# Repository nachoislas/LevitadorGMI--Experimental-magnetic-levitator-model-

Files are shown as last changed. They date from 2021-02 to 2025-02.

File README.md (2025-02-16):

# LevitadorGMI
El sistema de control de levitacion magnetica que se desarrolla en este proyecto tiene la finalidad de mantener en estado de levitacion a un objeto por medio de la utilizacion de un electroiman y una placa de control. El primero consta de dos piezas formadas por laminas de acero apiladas: una con forma de “E” , que se encuentra fijada desde arriba y tiene un bobinado de cobre en su rama central.

Link al la publicacion del proyecto [https://rinfi.fi.mdp.edu.ar/handle/123456789/722](https://rinfi.fi.mdp.edu.ar/handle/123456789/722)

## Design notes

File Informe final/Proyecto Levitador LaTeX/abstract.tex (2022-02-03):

%% !TeX spellcheck = en_GB
%
%Multiphase power converters have become a very attractive solution for the current control on high power applications, due to the power dissipation reduction in the active and passive components, and the improvement in the total ripple characteristics.
%
%These applications, which commonly arise in the high-energy physics field, require the control of high current (on the order of kiloamperes) with high precision (on the order of several hundreds of ppm). Additionally, large variations in the current reference and perturbations in the input or output voltages are present. These variations generate transient errors that have to be corrected in several hundreds of microseconds. Given the current level and the technological limitations of the semiconductor devices, the maximum allowable switching frequency implies transient times on the order of a few switching periods. Under these conditions, several requirements arise that cannot be satisfied by the existent current control techniques, due to their limited transient response, or sensitivity to the converter operating point or parasitic elements.
%
%According to these problematics, the present thesis studies the current control in multiphase power converters, and proposes solutions to achieve the transient and precision requirements above mentioned.
%
%The first proposal is the current ripple characterization, as a function of the differences across each phase inductance value. This characterization allows to find expressions for the total ripple that, unlike the methodologies present in the literature, are valid for any number of phases and duty cycle. These expressions allow to calculate others magnitudes, such as peak value, RMS value and the harmonic content of the total current ripple.
%
%The proposed characterization allows to develop a mitigation methodology that significantly improves the total current ripple in practical conditions, with respect to the only methodology present in the literature based on the same principle. This improvement is achieved without significantly increasing the calculation complexity.
%
%Finally, a current control for multiphase power converters is proposed. The proposed control is able to precisely track the current reference, and achieve transient times on the order of a few switching periods, under changes on the current reference or perturbations in the converter input or output voltages.
%
%The proposals have been validated by means of simulations or experimental measurements on a low-scale prototype.

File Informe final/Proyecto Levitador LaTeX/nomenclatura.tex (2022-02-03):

{
\renewcommand{\arraystretch}{0.8}
\begin{longtable}[l]{p{100pt} p{300pt}}
  $CCM$ & Modo de conducción continua \\
  & \textit{(Continous Conduction Mode)} \\
  $DCM$ & Modo de conducción discontinua \\
  & \textit{(Discontinous Conduction Mode)} \\
  $\pwm{x}$ & Señal de comando de la llave de la fase $x$ \\
  $PCMC$ & Control modo corriente pico \\
  & \textit{(Peak Current Mode Control)}\\
  $ACMC$ & Control modo corriente media \\
  & \textit{(Average Current Mode Control)}\\
  $PCPC$ & Control de punto de cruce proyectado \\
  & \textit{(Projected Cross Point Control)}\\    
  $SZCC$ & Control de cruce por cero sincronizado \\
  & \textit{(Synchronized Zero Crossing Control)} \\
  $IGBT$ & Transistor bipolar de puerta aislada \\
  & \textit{(Insulated Gate Bipolar Transistor)} \\
  $MOSFET$ & Transistor de efecto de campo metal-óxido-semiconductor \\ & \textit{(Metal-Oxide-Semiconductor Field-Effect Transistor)} \\
  $FPGA$ & Arreglo de compuertas programable en campo \\
  & \textit{(Field Programmable Gate Array)}
  
%  
%  	$\iref$                        & Referencia de corriente.\\
%  	$i_x$                            & Corriente de la fase $x$.\\
%  	$\ierr{x}$                         & Error de corriente de la fase $x$: $\ierr{x}=\iref-i_x$.                                      \\
%  	$\pwm{x}$                          & Señal de comando de la llave de la fase $x$. \\
%  	$V_{IN}$,$V_0$                   & Tensiones de entrada y salida.\\
%  	$\sync{x}$                  & Señ\\
%  	$T_{Sync}$                       & Synchronization signal period.                                                   \\
%  	$T_S$                            & Switching period.                                                                \\
%  	$t_e(k)$                         & Time error between $i_e$ zero crossing and syncronization signal at instant $k$. \\
%  	$t_{hp}(k+1)$                    & Next semi-period time: $t_{hp}(k+1)=\frac{T_{Sync}}{2}-t_e(k)$                   \\
%  	$t_{sw}(k+1)$                    & Interval between $i_e$ zero crossing and  $\pwm{i}$ switching instant.      \\ 
  \end{longtable}
}

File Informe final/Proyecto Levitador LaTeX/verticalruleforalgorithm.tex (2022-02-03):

% begin vertical rule patch for algorithmicx (http://tex.stackexchange.com/questions/144840/vertical-loop-block-lines-in-algorithmicx-with-noend-option)
\makeatletter
% start with some helper code
% This is the vertical rule that is inserted
    \newcommand*{\algrule}[1][\algorithmicindent]{\makebox[#1][l]{\hspace*{.5em}\thealgruleextra\vrule height \thealgruleheight depth \thealgruledepth}}%
% its height and depth need to be adjustable
\newcommand*{\thealgruleextra}{}
\newcommand*{\thealgruleheight}{.75\baselineskip}
\newcommand*{\thealgruledepth}{.25\baselineskip}

\newcount\ALG@printindent@tempcnta
\def\ALG@printindent{%
    \ifnum \theALG@nested>0% is there anything to print
        \ifx\ALG@text\ALG@x@notext% is this an end group without any text?
            % do nothing
        \else
            \unskip
            \addvspace{-1pt}% FUDGE to make the rules line up
            % draw a rule for each indent level
            \ALG@printindent@tempcnta=1
            \loop
                \algrule[\csname ALG@ind@\the\ALG@printindent@tempcnta\endcsname]%
                \advance \ALG@printindent@tempcnta 1
            \ifnum \ALG@printindent@tempcnta<\numexpr\theALG@nested+1\relax% can't do <=, so add one to RHS and use < instead
            \repeat
        \fi
    \fi
    }%
\usepackage{etoolbox}
% the following line injects our new indent handling code in place of the default spacing
\patchcmd{\ALG@doentity}{\noindent\hskip\ALG@tlm}{\ALG@printindent}{}{\errmessage{failed to patch}}
\makeatother

% the required height and depth are set by measuring the content to be shown
% this means that the content is processed twice
\newbox\statebox
\newcommand{\myState}[1]{%
    \setbox\statebox=\vbox{#1}%
    \edef\thealgruleheight{\dimexpr \the\ht\statebox+1pt\relax}%
    \edef\thealgruledepth{\dimexpr \the\dp\statebox+1pt\relax}%
    \ifdim\thealgruleheight<.75\baselineskip
        \def\thealgruleheight{\dimexpr .75\baselineskip+1pt\relax}%
    \fi
    \ifdim\thealgruledepth<.25\baselineskip
        \def\thealgruledepth{\dimexpr .25\baselineskip+1pt\relax}%
    \fi
    %\showboxdepth=100
    %\showboxbreadth=100
    %\showbox\statebox
    \State #1%
    %\State \usebox\statebox
    %\State \unvbox\statebox
    %reset in case the next command is not wrapped in \myState
    \def\thealgruleheight{\dimexpr .75\baselineskip+1pt\relax}%
    \def\thealgruledepth{\dimexpr .25\baselineskip+1pt\relax}%
}
% end vertical rule patch for algorithmicx

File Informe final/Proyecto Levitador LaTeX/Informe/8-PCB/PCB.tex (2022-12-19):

\chapter{Diseño del circuito impreso} \chapterlabel{Informe/8-PCB} \label{cap:PCB}

%En este capítulo se mencionan los criterios tenidos en cuenta para el diseño del circuito impreso. Además, se muestran los esquemáticos y las imágenes del PCB desarrollados para la implementación de la placa de control mediante el uso del software Altium Designer. 

%Por otra parte, se describen las consideraciones y circuitos utilizados para las fuentes de alimentación del sistema.

En este capítulo se describen las consideraciones y circuitos utilizados para las fuentes de alimentación del sistema. Ademas se mencionan cuales son los conectores, puntos de prueba y jumpers que posee el PCB.

Luego se mencionan los criterios tenidos en cuenta para el diseño del circuito impreso. Además, se muestran los esquemáticos y las imágenes del PCB desarrollados para la implementación de la placa de control mediante el uso del software Altium Designer.

\section{Fuentes de alimentación}

\subsection{Fuente de alimentación externa de 24 V}

La fuente externa se encarga de alimentar todo el circuito. Debe ser capaz de suministrar $24\:V$ y hasta $30\:A$. Para ello se puede utilizar una fuente de laboratorio o baterías. Esta fuente se conecta a la placa de control mediante una bornera dispuesta en el borde del PCB. Además, se agrega un fusible para proteger la placa ante sobre-consumo y un diodo para evitar que se dañe cuando se ingresa con polaridad invertida.

\subsection{Fuente de alimentación interna de 12 V}

La fuente de $12\:V$ se encarga de alimentar al regulador de $5\:V$ y al \textsl{driver} del puente H. Debido a los bajos consumos de potencia y bajo costo, se utiliza una fuente lineal. Por lo tanto, se decide utilizar el integrado L78M12CDT-TR.

\subsection{Fuente de alimentación interna de 5 V}

La fuente de $5\:V$ se encarga de alimentar los operacionales, el sensor de efecto Hall, el inversor y el regulador de tensión de $2.5\:V$. Debido a los bajos consumos de potencia y bajo costo, se utiliza una fuente lineal. Por lo tanto, se decide utilizar el integrado L78M05CDT.

\section{Conexión entre placa de control y microcontrolador}

Se utiliza un conector tipo DB9 hembra como vía de conexión para las distintas salidas y entradas digitales. Además, en la placa se dispone de un led que se enciende cuando  se detecta una correcta conexión con el microcontrolador.

\section{Puntos de prueba y jumpers}

Se agregan puntos de prueba sobre el PCB para poder medir señales de interés como las de control de los gates de los MOSFET del puente H, la salida del comparador con histéresis, la salida del derivador en la etapa del estimador, entre otros. Cada punto de prueba está referenciado en los esquemáticos como TP.

Por otro lado, se agregan jumpers con el objetivo de hacer mediciones a cada etapa por separado. Cada uno de ellos está referenciado en los esquemáticos como P.

\section{Esquemáticos}

\subsection{Principal}
\begin{figure}[H]
	\centering
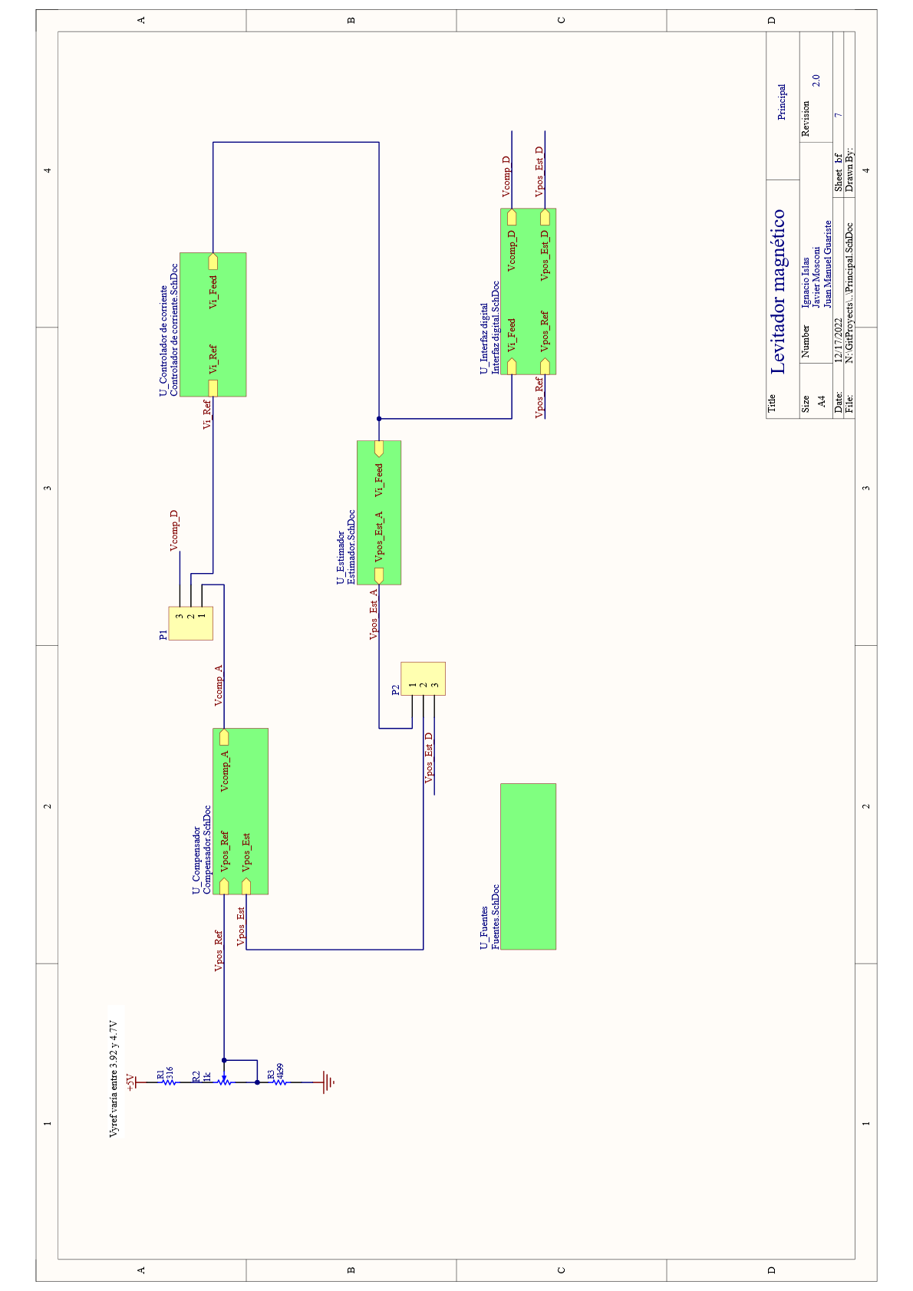
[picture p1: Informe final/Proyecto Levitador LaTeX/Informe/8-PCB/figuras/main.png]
	
	%\caption{Diagrama en bloques de la implementación digital.}
	\label{fig:main}
\end{figure}

\subsection{Controlador de corriente}
\begin{figure}[H]
	\centering
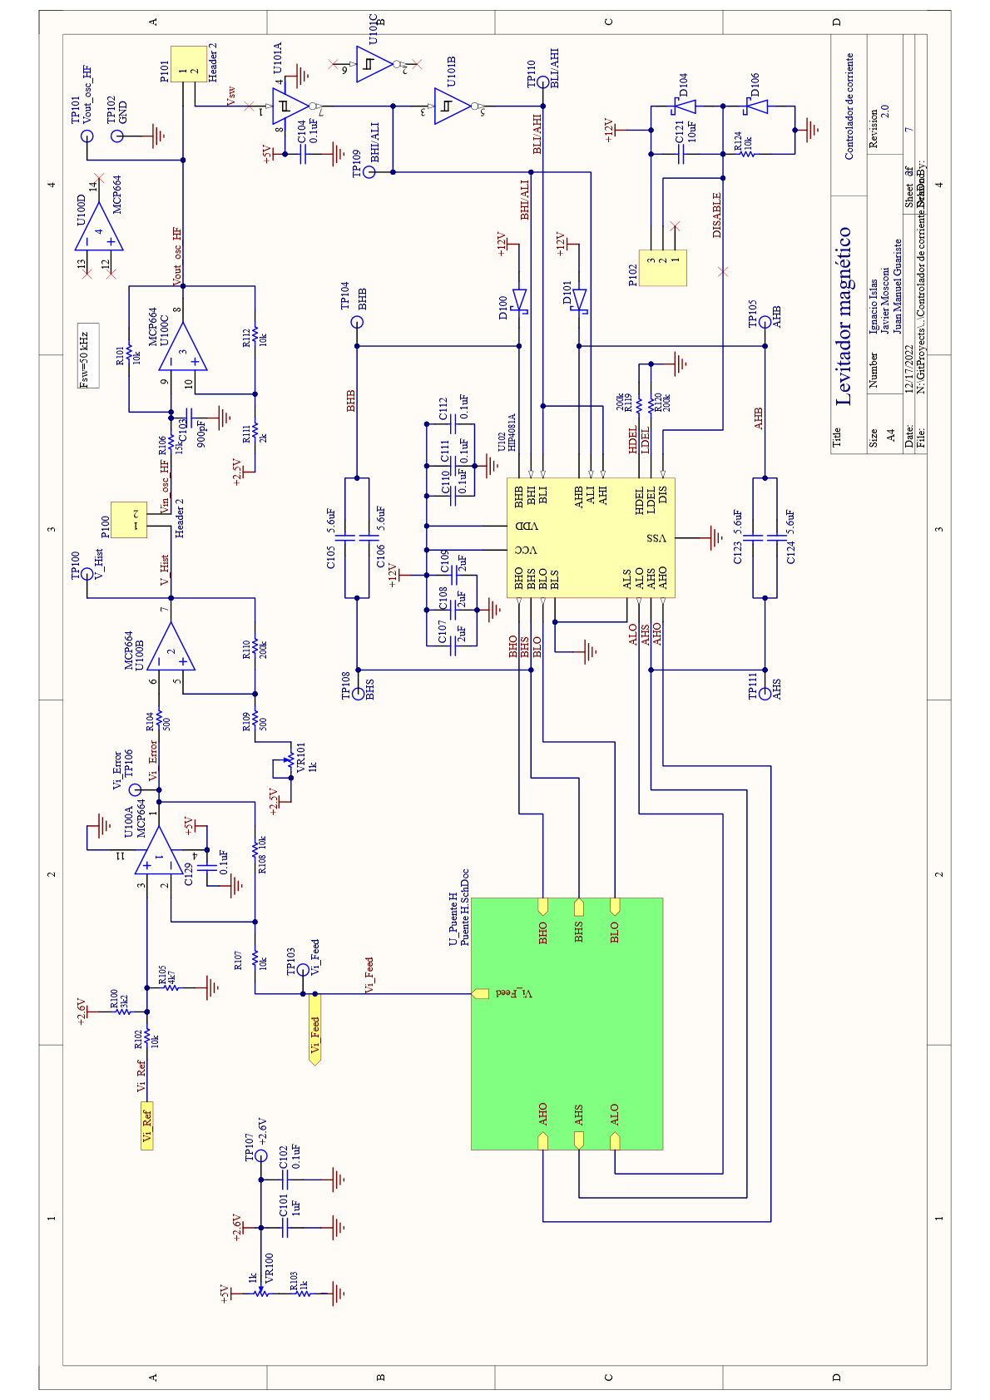
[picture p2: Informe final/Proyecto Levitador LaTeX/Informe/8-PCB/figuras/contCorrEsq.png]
	
	%\caption{Diagrama en bloques de la implementación digital.}
	\label{fig:contCorrEsq}
\end{figure}

\subsection{Puente H}
\begin{figure}[H]
	\centering
	
	%\caption{Diagrama en bloques de la implementación digital.}
	\label{fig:PuenteH}
\end{figure}

\subsection{Compensador analógico}
\begin{figure}[H]
	\centering
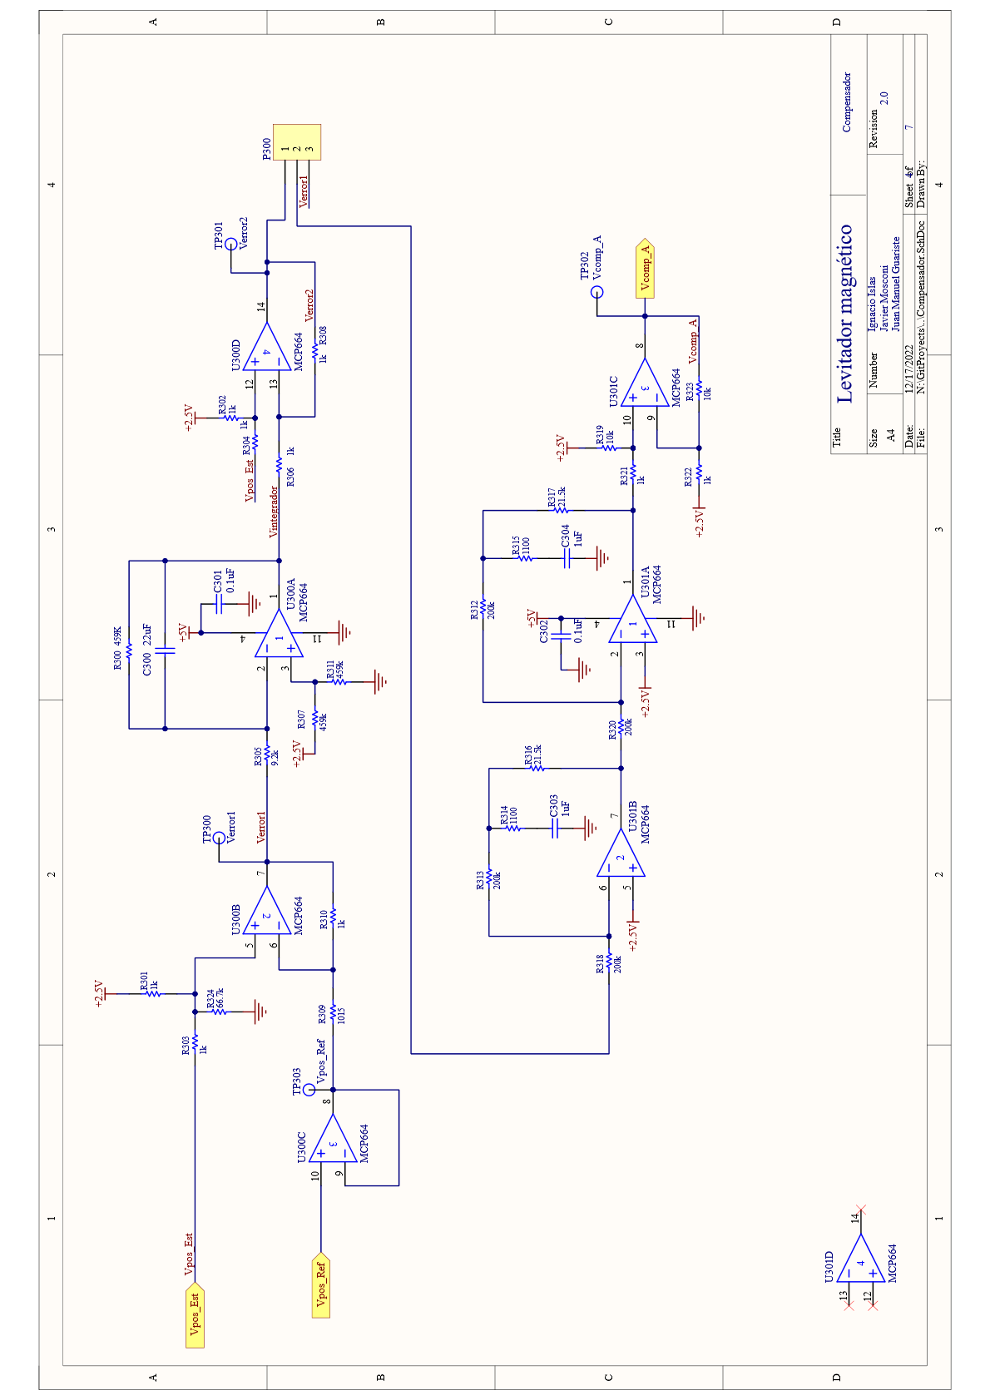
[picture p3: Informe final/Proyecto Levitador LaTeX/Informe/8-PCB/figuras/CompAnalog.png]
	
	%\caption{Diagrama en bloques de la implementación digital.}
	\label{fig:CompAnalog}
\end{figure}

\subsection{Estimador analógico}
\begin{figure}[H]
	\centering
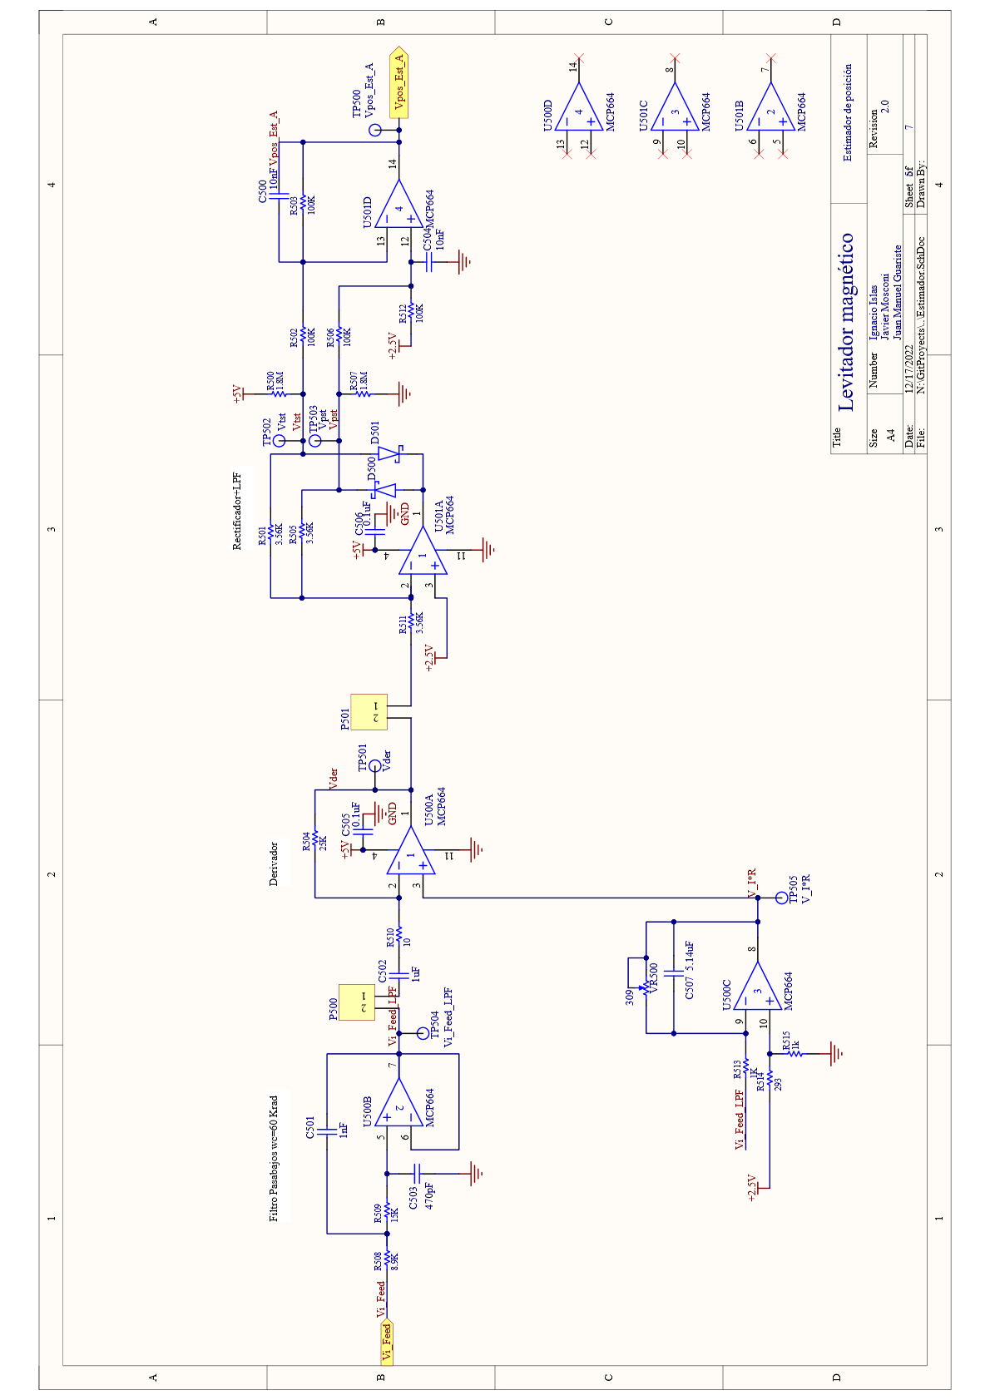
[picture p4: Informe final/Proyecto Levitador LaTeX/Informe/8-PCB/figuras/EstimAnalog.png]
	
	%\caption{Diagrama en bloques de la implementación digital.}
	\label{fig:EstimAnalog}
\end{figure}

\subsection{Interfaz con microcontrolador}
\begin{figure}[H]
	\centering
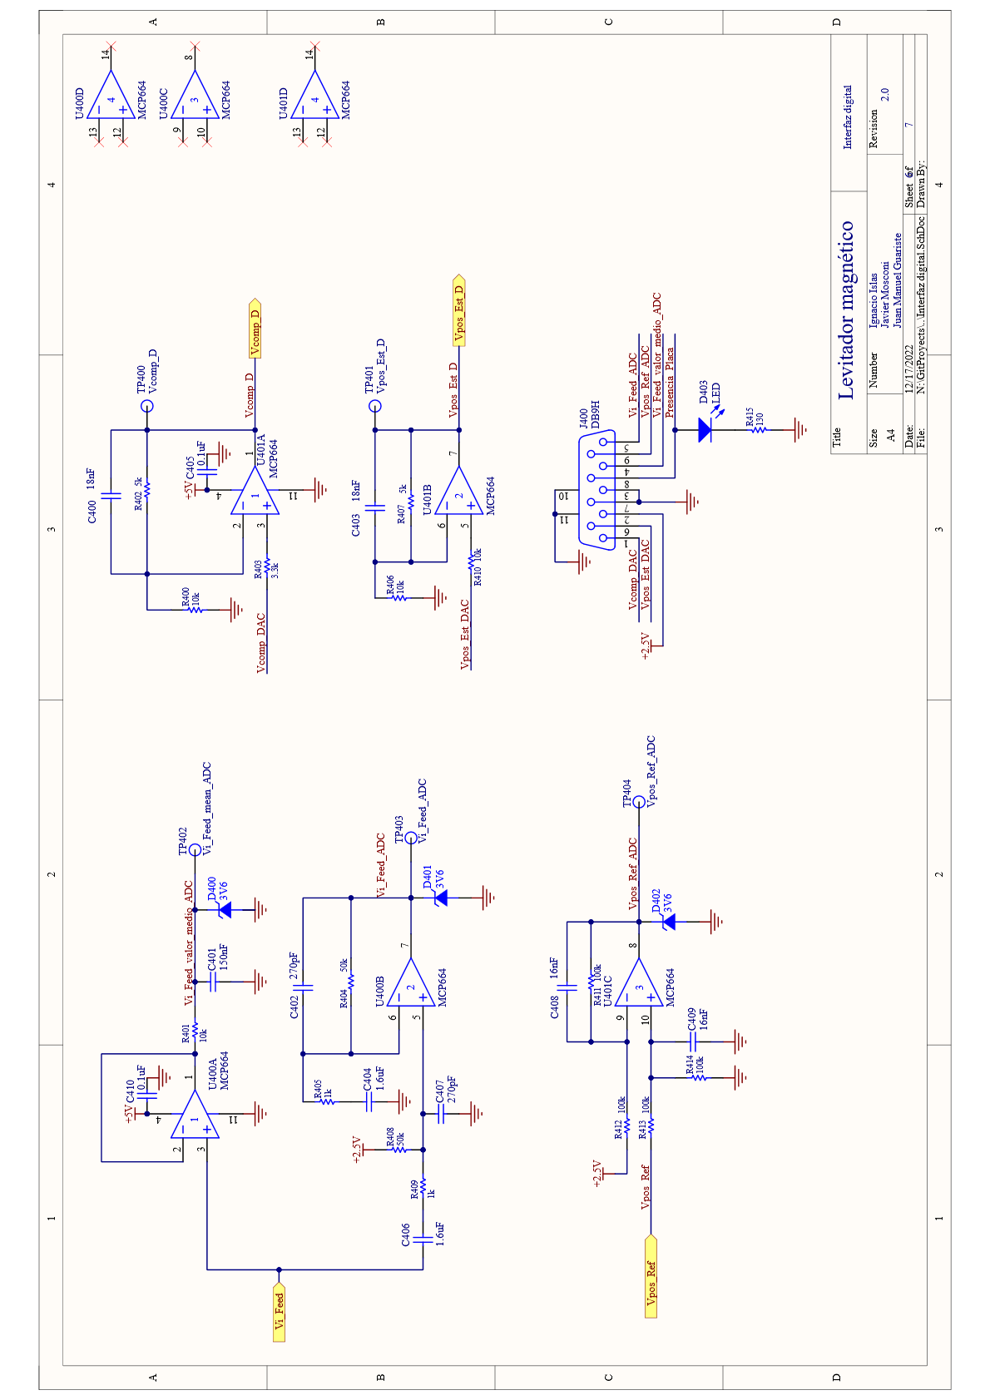
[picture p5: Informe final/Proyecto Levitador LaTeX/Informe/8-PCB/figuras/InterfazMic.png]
	
	%\caption{Diagrama en bloques de la implementación digital.}
	\label{fig:InterfazMic}
\end{figure}

\subsection{Fuentes de alimentación}
\begin{figure}[H]
	\centering
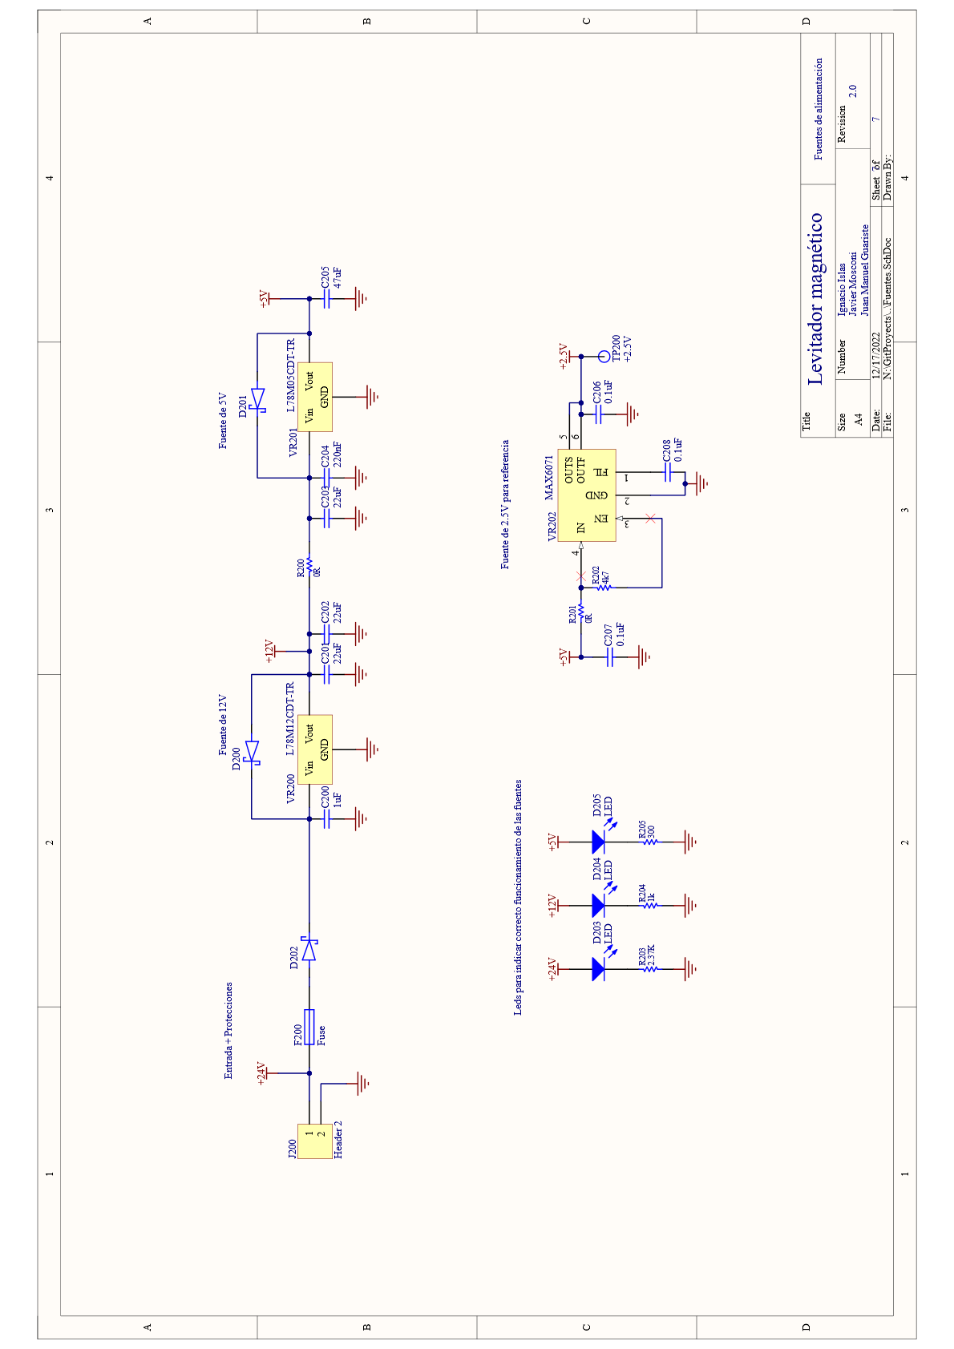
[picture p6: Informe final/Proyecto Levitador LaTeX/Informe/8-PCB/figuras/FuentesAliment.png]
	
	%\caption{Diagrama en bloques de la implementación digital.}
	\label{fig:FuentesAliment}
\end{figure}

\section{PCB}
\subsection{Consideraciones para el diseño del PCB}
Para el diseño del PCB se tuvieron en cuenta los siguientes aspectos:

\begin{itemize}
	\item Se realizó el diseño en una placa de 2 capas para reducir el costo de fabricación.
	\item Se utilizó un plano de masa para la etapa de potencia y otro para el resto del circuito. Se intentó reducir al mínimo las conexiones entre ambos planos con el objetivo de disminuir el ruido inducido por la etapa de potencia en el resto del circuito.
	\item Se mantuvo separada la etapa de potencia con las de pequeña señal.
	\item Se intentó reducir al mínimo la longitud de las pistas de las señales críticas como la tensión de salida del sensor de efecto Hall.
	\item Se utilizaron pistas gruesas y polígonos para la etapa de potencia que deben soportar la circulación de corrientes elevadas.
	\item Se quitó la capa \textsl{Top Solder} en la etapa de potencia correspondiente al puente H para mejorar la disipación.
	\item Se utilizaron vias stitching en los planos de masa sobre la placa para mejorar la aislación entre componentes y reducir el acople por campos electromagnéticos.
	\item Se ``acostaron'' los MOSFET sobre la placa para ayudar a su disipación de potencia.
	\item Para optimizar el tamaño de la placa, se rutearon las pistas de manera organizada. Para ello, se intentó que las pistas verticales se realicen en la capa superior mientras que las horizontales, en la inferior.
	\item El proyecto se dividió en 7 esquemáticos. Cada uno de ellos se asocia a una etapa en específico (compensación analógica, controlador de corriente, estimador analógico, etc). 
	\item  Los componentes de cada esquemático tiene asociado un rango de valores determinados para los \textsl{designators}. Es decir, todos los componentes con \textsl{designators} entre 0 y 99 pertenecen al primer esquemático, los de 100 a 199 al segundo, y así sucesivamente.  De esta forma, con solo ver el \textsl{designators} en el PCB es posible determinar, fácilmente, a qué etapa pertenece.  
	\item Se siguieron las reglas de diseño estándar de PCBWay.
	
\end{itemize}

\subsection{Modelo 2D}
\subsubsection{Vista superior}
\begin{figure}[H]
	\centering
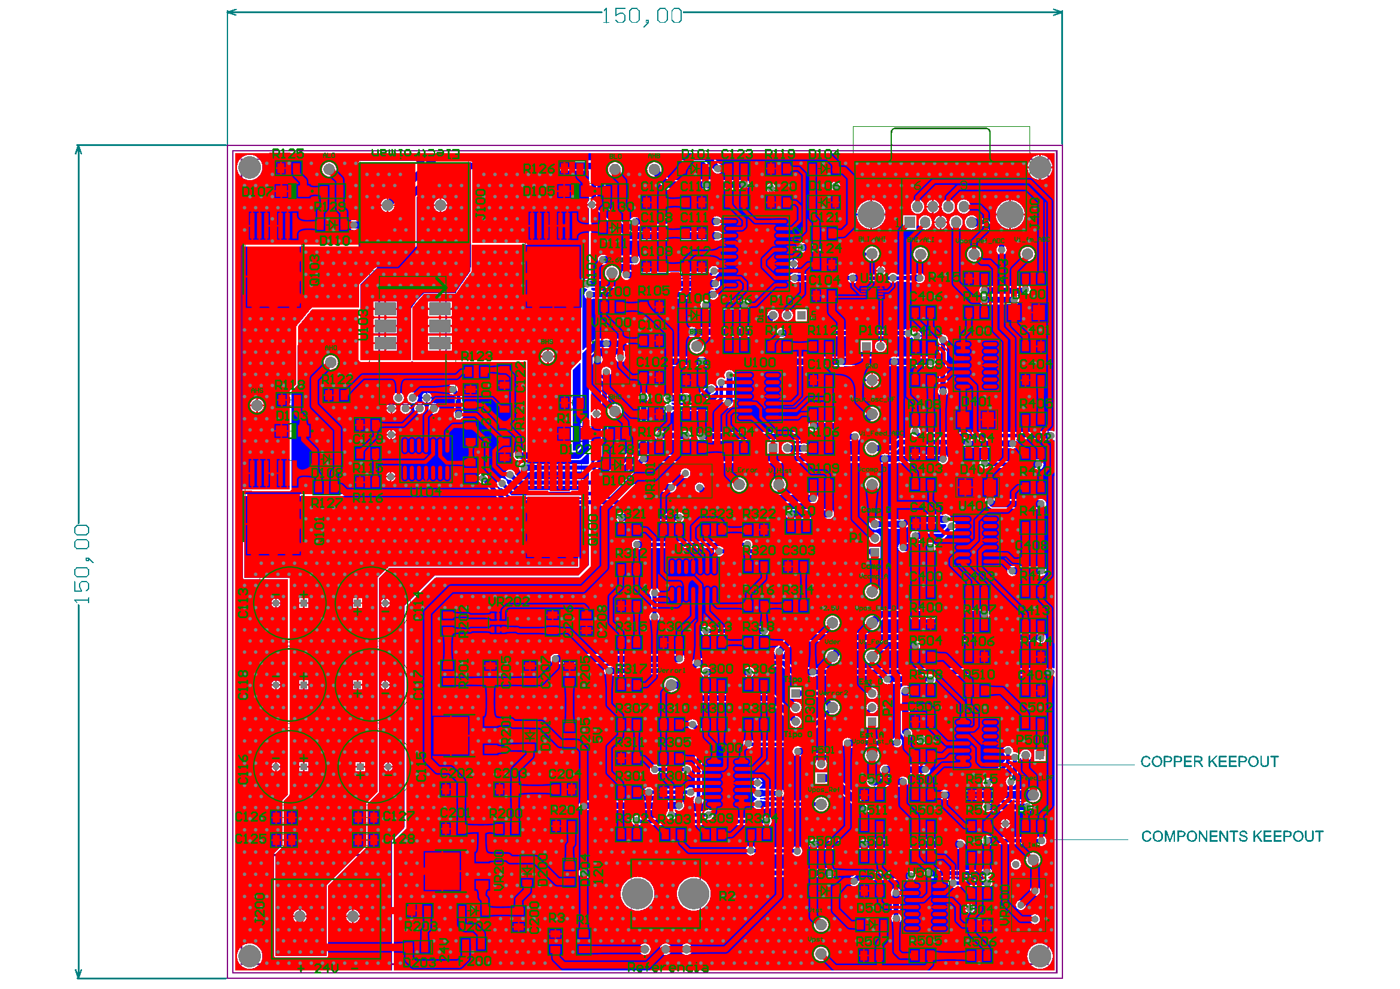
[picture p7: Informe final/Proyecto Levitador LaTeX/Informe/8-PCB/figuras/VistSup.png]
	
	%\caption{Diagrama en bloques de la implementación digital.}
	\label{fig:VistSup}
\end{figure}

\subsubsection{Vista inferior}
\begin{figure}[H]
	\centering
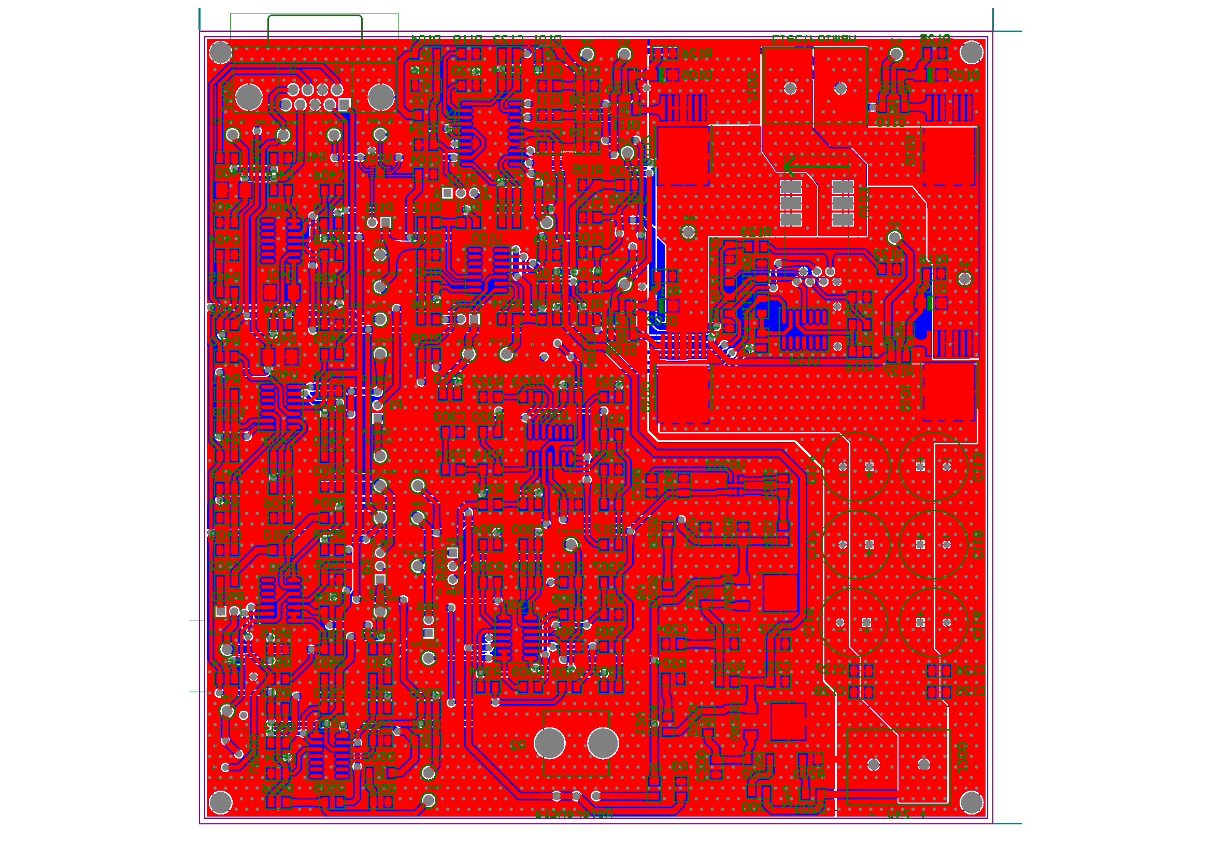
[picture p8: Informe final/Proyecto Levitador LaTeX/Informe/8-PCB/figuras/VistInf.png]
	
	%\caption{Diagrama en bloques de la implementación digital.}
	\label{fig:VistInf}
\end{figure}

\subsection{Modelo 3D}
\subsubsection{Vista superior}
\begin{figure}[H]
	\centering
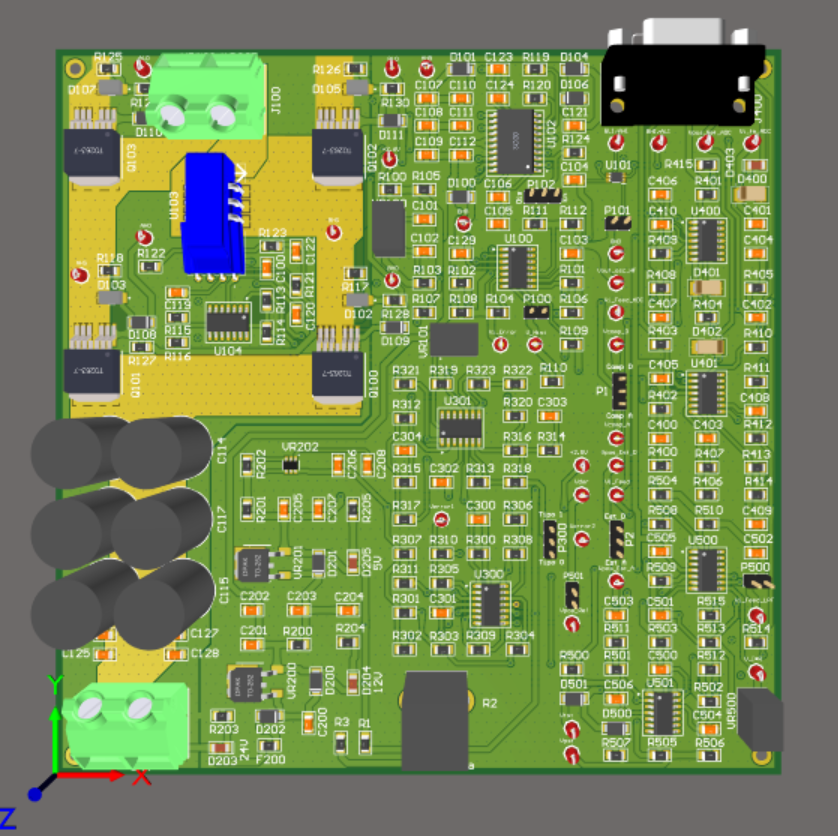
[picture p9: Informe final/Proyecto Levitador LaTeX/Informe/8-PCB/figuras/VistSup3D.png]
	
	%\caption{Diagrama en bloques de la implementación digital.}
	\label{fig:VistSup3D}
\end{figure}

\subsubsection{Vista inferior}
\begin{figure}[H]
	\centering
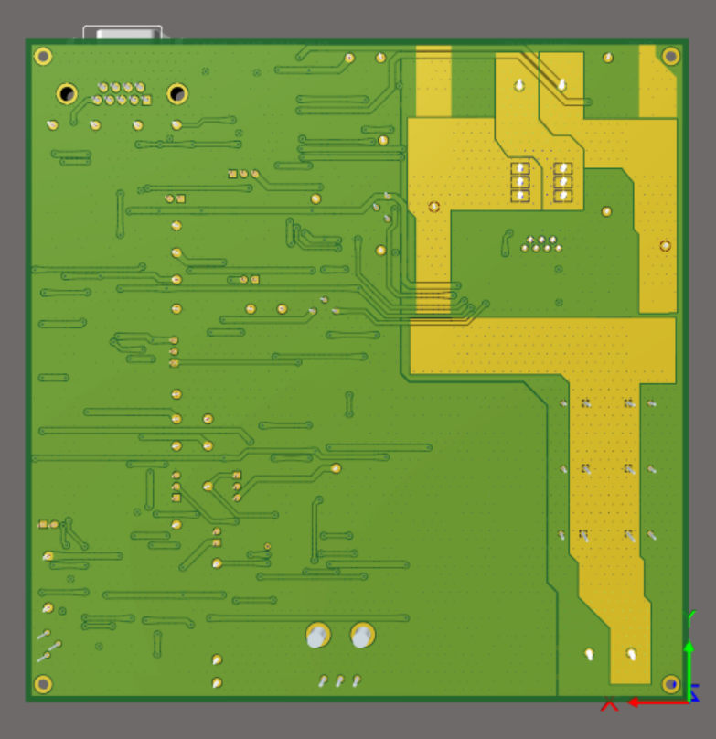
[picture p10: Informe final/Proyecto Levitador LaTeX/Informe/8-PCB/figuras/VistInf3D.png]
	
	%\caption{Diagrama en bloques de la implementación digital.}
	\label{fig:VistInf3D}
\end{figure}

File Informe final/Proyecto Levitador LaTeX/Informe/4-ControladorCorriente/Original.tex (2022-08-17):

\chapter{Controlador de corriente} \chapterlabel{Informe/4-ControladorCorriente} \label{cap:ControladorCorriente}

En este capítulo se diseña y modela el circuito encargado de controlar la corriente que circula por el electroimán. Debido a que el sistema trabaja con corrientes elevadas se implementan estrategias de conmutación con el fin de reducir las pérdidas de energía. Para ello se utiliza una topología de puente H con cuatro MOSFET y un \textsl{bootstrap driver} que los controla. Además, se detallan los criterios tenidos en cuenta al momento de  elegir  y dimensionar todos los componentes que intervienen para lograr el correcto funcionamiento del controlador de corriente. Por último, se obtiene su función transferencia  para ser utilizada en el diseño del compensador.

\section{Descripción general}

\noindent Para regular la fuerza ejercida por el electroimán es necesario controlar la corriente que circula por él. Para ello, se modela a la planta como la admitancia de un circuito RL serie, cuya inductancia varía con el entrehierro como se observa en la expresión \ref{eq_admitancia}.

\begin{equation} \label{eq_admitancia}
\frac{1}{sL(Y_g)\ +\ R_L}
\end{equation}

\noindent Para realizar este control se utiliza un sistema realimentado, como el que se muestra en la figura \ref{fig:img_diag-en-bloques}. La entrada al sistema es una tensión de referencia ($V_{iLRef}$) proporcional a la corriente de salida deseada, que luego se multiplica por la ganancia de entrada ($K_{in}$). La corriente del electroimán se realimenta en forma de una tensión proporcional a ella ($V_{iLF}$). Ambas tensiones son restadas y el resultado ($V_e$) ingresa al bloque del comparador con histéresis, que actúa en conmutación, por lo que su salida tiene dos estados posibles: $\pm$$V_L$.

\noindent Al ser aplicadas al inductor se produce una rampa de corriente: si la tensión es positiva, la rampa crece, y si es negativa decrece. De esta forma, debido a la conmutación del comparador se obtiene, a la salida, una forma de onda triangular $I_L$, cuyo valor medio es la corriente deseada y es proporcional a la tensión de referencia.

\begin{figure}[H]
	\centering
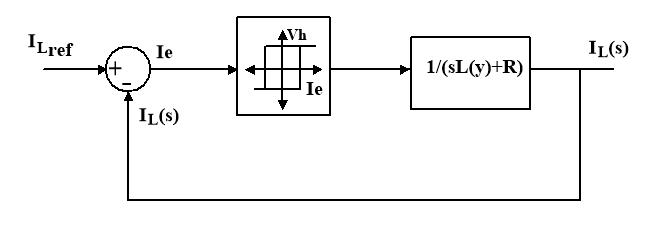
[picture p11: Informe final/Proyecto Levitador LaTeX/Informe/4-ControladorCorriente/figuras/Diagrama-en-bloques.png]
	
	\caption{Diagrama en bloques simplificado del controlador de corriente.}
	\label{fig:img_diag-en-bloques}
\end{figure}

\section{Circuito del controlador de corriente}

\noindent Se plantea la etapa de entrada que consiste en la ganancia $K_{in}$ y el restador con la señal realimentada. El objetivo es que una tensión de referencia en la entrada entre $0\:V$ y $5\:V$ se corresponda de manera lineal con una corriente de salida entre $0\:A$ y $30\:A$ (en valor medio). Por lo tanto, se obtiene una ganancia del controlador de corriente de $6\:A/V$. Para sensar la corriente se eligió utilizar un sensor de efecto Hall HO 15-NP \cite{HO15-NP} cuya transconductancia es de $H(s) = 53.3\:mV/A$. De esta manera la ganancia de entrada se calcula como:

\begin{equation}
	K_{in}=\frac{30\:A*53.3\:mV/A}{5\:V}=0.32 
\end{equation}

La salida de esta etapa, al igual que la tensión de salida del sensor de efecto Hall, se polarizan en un punto de operación de $2.6\:V$ (ver sección \ref{secc_justificación-puente-H}). Para lograrlo se utiliza un circuito como el que se muestra en la figura \ref{fig:img_etapa-de-entrada}.

\begin{figure}[H]
	\centering
	
	\caption{Etapa de entrada.}
	\label{fig:img_etapa-de-entrada}
\end{figure}

Para la implementación del comparador con histéresis se utiliza un amplificador operacional realimentado positivamente. Se eligió que la corriente de salida del electroimán tenga un ripple de $500\:mA$. Por lo tanto, al afectar este valor por la transconductancia del sensor de efecto Hall, se obtiene un ancho de histéresis de $26.665\:mV$, alrededor de un punto de operación de $2.5\:V$. El circuito implementado se muestra en la figura \ref{fig:img_comp-con-hist}.

\begin{figure}[H]
	\centering
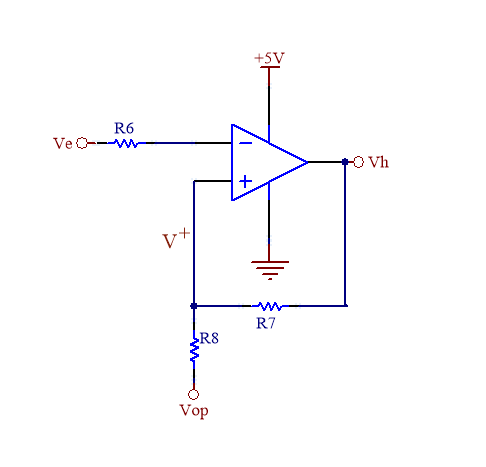
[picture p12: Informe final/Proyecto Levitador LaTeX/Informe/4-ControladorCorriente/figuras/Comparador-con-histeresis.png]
	
	\caption{Comparador con histéresis.}
	\label{fig:img_comp-con-hist}
\end{figure}

Para controlar la corriente se utiliza un \textsl{driver} que trabaja en conmutación con una topología en puente H con cuatro N-MOS. Este permite conmutar la polaridad de la tensión aplicada al electroimán entre $+24\:V$ para el estado ON y $-24\:V$ para el OFF. 

Para poder realizar simulaciones se modela al sensor de efecto Hall como una fuente de tensión controlada por corriente con una ganancia de $53.3\:mV/A$, cuya salida es realimentada a la etapa de entrada luego de restarle la tensión de referencia  $V_{bias}$ de $2.5\:V$, como se muestra en la figura \ref{fig:img_resta-Vbias}.

La implementación circuital de estas dos etapas puede observarse en la figura \ref{fig:img_puenteH}. 

\begin{figure}[H]
	\centering
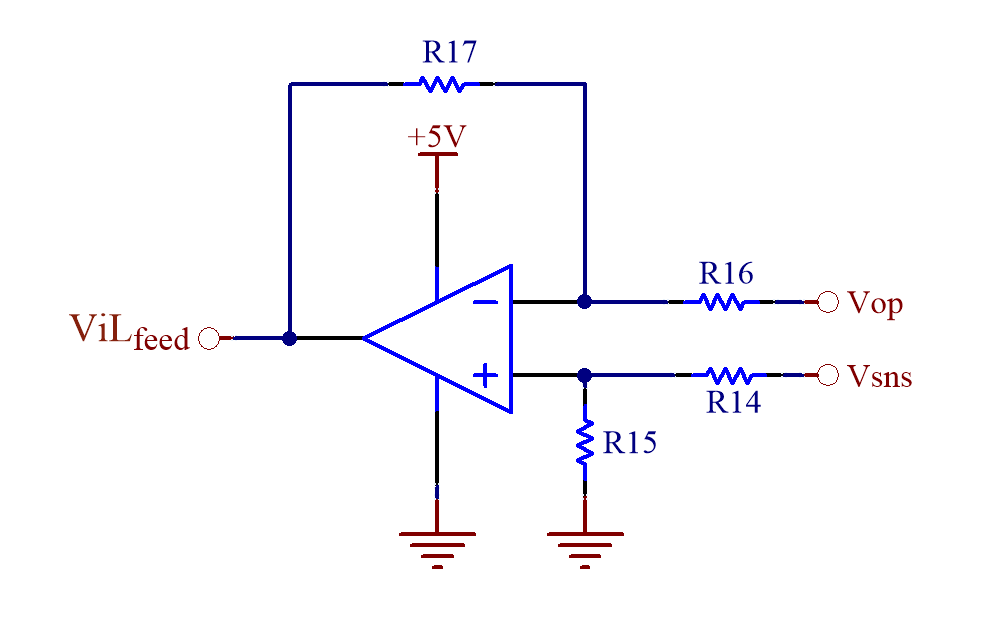
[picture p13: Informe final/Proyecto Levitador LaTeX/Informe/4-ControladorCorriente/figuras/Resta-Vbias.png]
	
	\caption{Resta de $V_{bias}$ al sensor de efecto Hall.}
	\label{fig:img_resta-Vbias}
\end{figure}

\begin{figure}[H]
	\centering
	
	\caption{Puente H y sensor de efecto Hall.}
	\label{fig:img_puenteH}
\end{figure}

\subsection{Simulaciones de formas de onda}

\noindent En la figura \ref{fig:img_formas-de-onda-corriente} se pueden observar dos formas de onda. La inferior  corresponde a la tensión de salida del comparador con histéresis y la superior a la corriente que circula por el electroimán. Para la simulación se utilizó una tensión de referencia de entrada de $1\:V$, por lo que el valor medio de la corriente en la salida es $6\:A$ con un ripple de $500\:mA$.

\begin{figure}[H]
	\centering
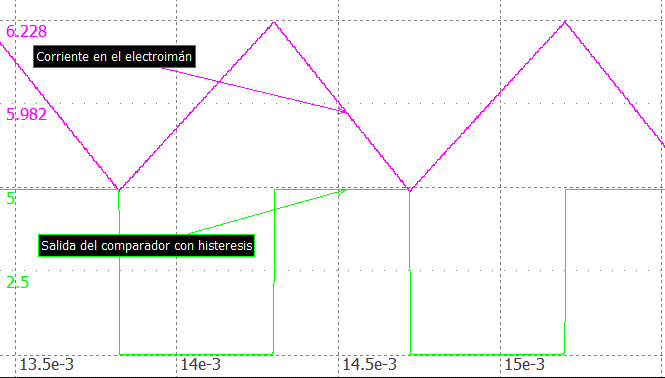
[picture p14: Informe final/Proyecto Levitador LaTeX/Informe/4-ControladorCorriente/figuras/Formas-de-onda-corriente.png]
	
	\caption{Formas de onda de corriente en el electroimán y tensión de salida del comparador.}
	\label{fig:img_formas-de-onda-corriente}
\end{figure}

\subsection{Simulación de un escalón en la referencia de corriente}

\noindent En la figura \ref{fig:img_respuesta-al-escalon} se muestra cómo cambia la corriente en el electroimán al aplicarle a la entrada del controlador un escalón de tensión entre $1\:V$ y $3\:V$. Se puede observar cómo la conmutación del comparador se detiene para ajustar la corriente con la referencia.

\begin{figure}[H]
	\centering
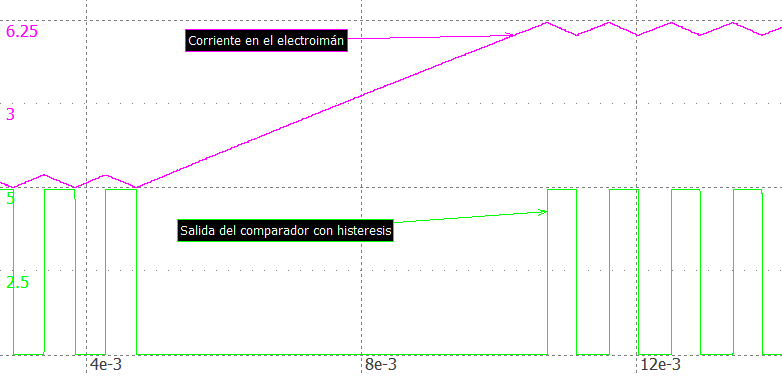
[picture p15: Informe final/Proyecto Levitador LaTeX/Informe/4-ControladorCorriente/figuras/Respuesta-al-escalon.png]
	
	\caption{Respuesta al escalón del circuito.}
	\label{fig:img_respuesta-al-escalon}
\end{figure}

\subsection{Descripción general de la topología}

\noindent Se desea controlar la corriente que circula por el electroimán y, debido a que el sistema va a trabajar con corrientes elevadas, es importante que la implementación del controlador de corriente sea eficiente. Por lo tanto, para disminuir la disipación de potencia del circuito se utiliza un controlador que funciona en conmutación. 

\noindent Para lograr una corriente contínua en el electroimán mediante una fuente conmutada se debe alternar la polaridad de la tensión aplicada en los bornes del inductor. De esta forma, la corriente crece y decrece (según la polaridad) con forma exponencial debido a la resistencia interna del electroimán. Sin embargo, como el intervalo de tiempo de esta conmutación es pequeño comparado con la constante de tiempo de la planta, el incremento de corriente será pequeño y puede ser aproximado a una recta. Por lo tanto, se obtiene una corriente contínua con un ripple superpuesto de forma triangular. 

\noindent Para lograr alternar la polaridad de la fuente sobre el inductor se utiliza una topología en puente H con cuatro MOSFET manejados por el controlador por histéresis como se observa en la figura \ref{fig:img_topologia-puenteH}. Pueden diferenciarse dos semiciclos de trabajo: uno de estado ON y otro de estado OFF. El primero se define como el semiciclo durante el cual la corriente en el inductor crece (pendiente positiva), mientras que el segundo se da cuando la corriente decrece.

\begin{figure}[H]
	\centering
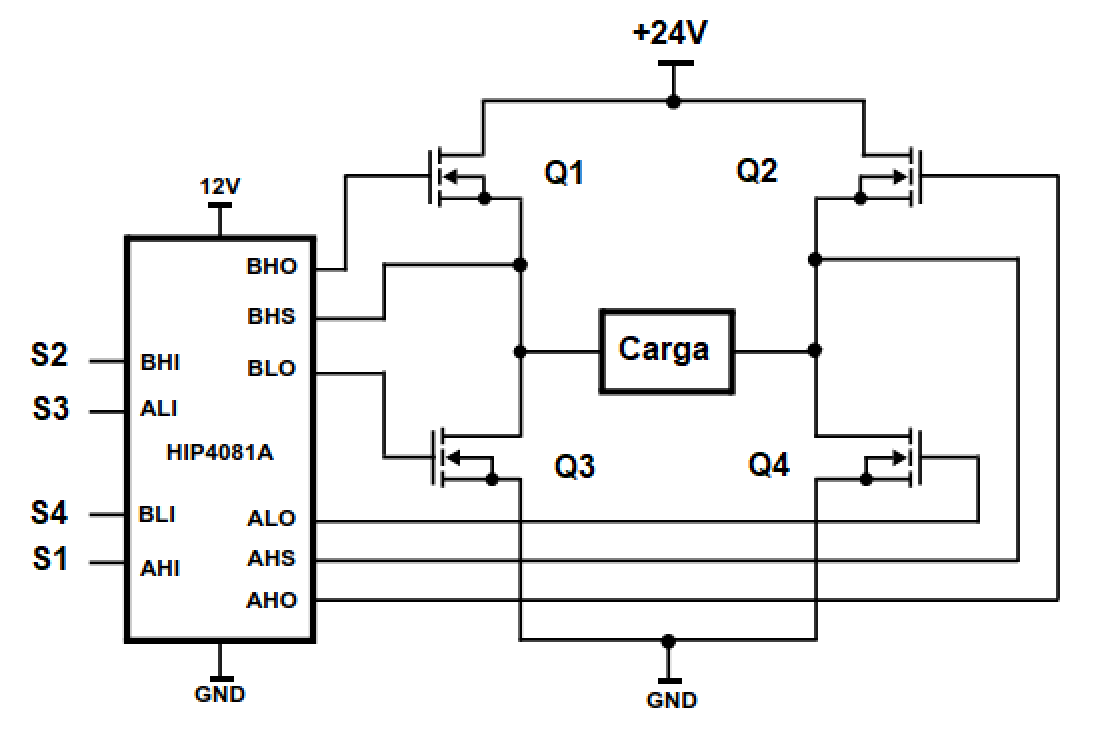
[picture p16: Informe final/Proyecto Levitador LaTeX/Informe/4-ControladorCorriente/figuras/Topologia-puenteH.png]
	
	\caption{Topología elemental del puente H.}
	\label{fig:img_topologia-puenteH}
\end{figure}

\noindent El electroimán se conecta entre los puntos medios de cada par de transistores. De esta manera se puede conmutar la polaridad de la tensión que se le aplica. Sólo se permite que dos transistores se enciendan a la vez, y esto se realiza de manera diagonal. Es decir, en la figura \ref{fig:img_topologia-puenteH}, $Q_1$ y $Q_4$ pueden estar encendidos, mientras que $Q_3$ y $Q_2$ están apagados, y viceversa. De otra forma, se podría generar un cortocircuito entre la fuente de alimentación y GND, que produciría una circulación de corriente denominada \textsl{shoot-through}. 

\noindent Los cuatro MOSFET utilizados para el puente H son de tipo N. Para que estos puedan funcionar correctamente en conmutación es necesario que en el estado ON, la diferencia de tensión entre \textsl{gate} y \textsl{source} sea mayor o igual a $7\:V$. Esto no es un problema para los dos MOS inferiores del puente H ($Q_2$ y $Q_4$), ya que la tensión en \textsl{source} está fijada en GND y el \textsl{driver} puede aplicar $12\:V$ al \textsl{gate} (superando los $7\:V$ entre \textsl{gate} y \textsl{source}). El problema radica en los transistores superiores del puente H, ya que la tensión en \textsl{source} varía entre $0\:V$ y $24\:V$, por lo que en el \textsl{gate} debería haber, por lo menos, $31\:V$ con respecto a GND. Sin embargo, la tensión máxima disponible entregada por la fuente es de $24\:V$. Para resolver este problema se utiliza un \textsl{driver} flotante con \textsl{bootstrap}.

\noindent Para controlar la conmutación se utiliza un MOSFET \textsl{driver} HIP4081A \cite{HIP4081A_FN3659} que se encarga de encender y apagar los transistores según las entradas de control. Además permite la configuración de un tiempo muerto para evitar que se enciendan dos transistores de un lado a la vez. También provee la circuitería necesaria para implementar la fuente flotante que enciende los MOSFET del lado superior para lo cual solo se debe agregar un diodo y un capacitor de manera externa. Para la implementación circuital se van a utilizar los MOSFET IPB160N04 \cite{IPB160N04}.

\noindent En la figura \ref{fig:img_bootstrap} se observa solo una de las mitades del puente H (lado A)  junto con las señales de control provistas por el \textsl{driver} HIP4081A. El análisis para la otra mitad es análogo, por lo que se evita por simplicidad. La implementación del \textsl{bootstrap driver} permite obtener en el \textsl{gate} del MOS superior, una tensión de $36\:V$ respecto a GND, de manera que se logra una diferencia de tensión mayor a $7\:V$ entre \textsl{gate} y \textsl{source}. 

\begin{figure}[H]
	\centering
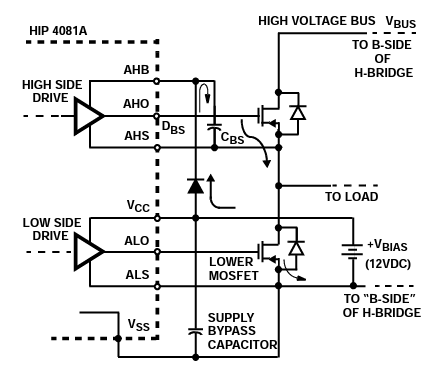
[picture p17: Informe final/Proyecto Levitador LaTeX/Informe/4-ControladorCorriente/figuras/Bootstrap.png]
	
	\caption{Configuración \textsl{bootstrap} simplificada.}
	\label{fig:img_bootstrap}
\end{figure}

\noindent El \textsl{bootstrap driver} consiste en un capacitor ($C_{BS}$), un diodo, y la circuitería interna del HIP4081A. Para garantizar el correcto funcionamiento del \textsl{bootstrap}, al encender el sistema, la secuencia de inicio del HIP4081A enciende las dos salidas de la parte inferior del puente H: ALO y BLO con el fin de encender $Q_2$ y $Q_4$ durante un tiempo que se conoce como periodo de refresco de \textsl{bootstrap}. De esta forma, los capacitores de \textsl{bootstrap} de ambos lados quedan conectados entre $12\:V$ y GND y se pueden cargar completamente. Durante este tiempo, las salidas a los \textsl{gates} AHO y BHO se mantienen en bajo continuamente lo que asegura que no se produzca corriente de \textsl{shoot-through} durante el período nominal de refresco del \textsl{bootstrap}. Una vez finalizado, las salidas responden normalmente al estado de las señales de entrada de control.

\noindent Para comprender su funcionamiento se hará un breve análisis del sistema. Para ello, se parte de la suposición de que el sistema se encuentra en funcionamiento: con el transistor $Q_2$ encendido (ALO = $V_{CC}$), $Q_1$ apagado (AHO = AHS = $0\:V$) y la corriente circulando de izquierda a derecha como lo indica la figura \ref{fig:img_bootstrap}. En ese caso, el capacitor $C_{BS}$ se carga a $12\:V$, ya que en un terminal tiene la fuente de $12\:V$ (a través del diodo $D_{BS}$) y el otro está conectado a GND por medio de $Q_2$.

\noindent Una vez que se apaga el transistor inferior, empieza a transcurrir el tiempo muerto. Debido a que la carga es inductiva, el valor medio de la corriente mantiene su sentido y circula por los diodos antiparalelos del MOS inferior del lado A y el superior del lado B. Esto provoca que el \textsl{source} del MOS superior del lado A tenga una tensión negativa igual a la caída de tensión en directa del diodo antiparalelo de $Q_2$. 

\noindent Una vez finalizado el tiempo muerto, se enciende el MOS $Q_1$. Para ello, la señal AHO se pone en nivel alto. Durante el tiempo que $Q_1$ pasa de estar apagado a encendido, la tensión en el \textsl{source} cambia de $-V_d$ a $V_{bus}$ de manera gradual mientras se carga el \textsl{gate}, y AHO pasa a ser igual a AHB, que es igual a la tensión entregada por el capacitor de \textsl{bootstrap} sumada a la tensión en el \textsl{source} de $Q_1$. De esta manera se logra una tensión de $36\:V$ con respecto a GND en el \textsl{gate} y genera una diferencia entre \textsl{gate} y \textsl{source} de $12\:V$.

\noindent Para lograr un funcionamiento adecuado del \textsl{bootstrap} es necesario dimensionar correctamente al capacitor $C_{BS}$ con el fin de que pueda proveer la carga suficiente durante el tiempo en el que el MOS esté encendido.

\subsection{Dimensionamiento de capacitor de \textsl{bootstrap}}

\noindent Para el dimensionamiento de los capacitores de \textsl{bootstrap} se tuvieron en cuenta sugerencias y procedimientos descriptos en \cite{HIP4081A_AN9405} y \cite{HIP4081A_FN3659}.

\noindent Para encender un NMOS es necesario proveer corriente a su \textsl{gate} hasta cargar las capacidades parásitas entre \textsl{gate-source} y \textsl{gate-drain}. Una vez cargadas, el MOS queda en estado encendido y no consume más corriente en el \textsl{gate}. En el caso de los MOS del lado superior, esta corriente proviene del capacitor de \textsl{bootstrap}. 

\noindent En la implementación del puente H se decidió colocar resistencias entre \textsl{gate} y \textsl{source} (ver apartado \ref{secc_res_gate_source}), que aparecen como $R_1$, $R_2$, $R_3$ y $R_4$ en la figura \ref{fig:img_capacitores-puenteH}. Debido a la diferencia de tensión entre \textsl{gate-source}, se genera una corriente constante en estas resistencias durante el tiempo que el MOS esté encendido, que también debe ser provista por el  \textsl{bootstrap}.

\begin{figure}[H]
	\centering
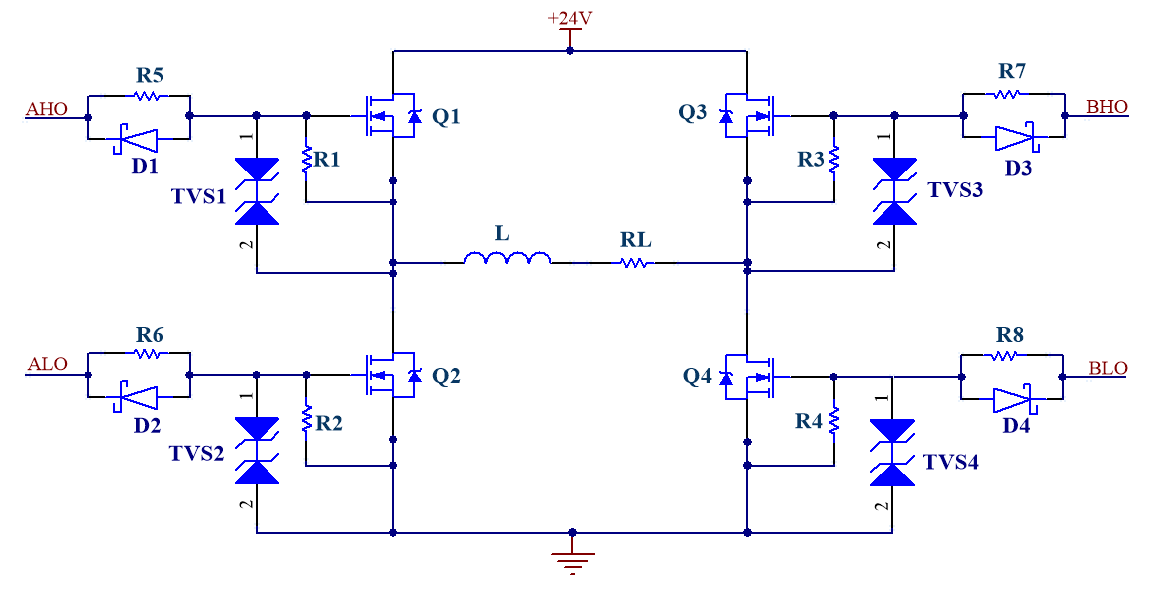
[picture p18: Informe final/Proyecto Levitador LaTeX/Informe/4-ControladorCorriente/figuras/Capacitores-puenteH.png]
	
	\caption{Puente H.}
	\label{fig:img_capacitores-puenteH}
\end{figure}

\noindent Por otro lado, el capacitor debe entregar corriente al diodo de \textsl{bootstrap} cuando este queda en inversa ($I_{DR}$), y también entregar una corriente de fuga al circuito integrado HIP ($I_{QBS}$). Esta última se desprecia ya que es compensada internamente por la bomba de carga del HIP.

\noindent Por lo tanto, para poder dimensionar correctamente el capacitor de \textsl{bootstrap} es necesario tener en cuenta todos los efectos mencionados anteriormente. Para ello se parte planteando la carga que almacena el capacitor \textsl{bootstrap}:

\begin{equation} \label{eq_carga-cap-bootstrap}
Q_{BS}=C_{BS}*\Delta V_{BS}
\end{equation}

\noindent En la ecuación \ref{eq_carga-cap-bootstrap}, $Q_{BS}$ es la carga total del capacitor de \textsl{bootstrap}, $C_{BS}$ su capacidad, y $\Delta V_{BS}$ es la diferencia de  tensión entre sus terminales. 

\noindent Para evitar sufrir una caída de tensión tal que afecte el encendido de los MOS, es necesario que $Q_{BS}$ pueda abastecer también al \textsl{gate}, al diodo en inversa y a la resistencia entre \textsl{gate-source}. Por lo tanto:

\begin{equation} \label{eq_carga-cap-bootstrap2}
Q_{BS} > Q_G + Q_{RR} + \frac{I_{DR}+I_{GS}}{f_{PWM}}
\end{equation}

\noindent Donde:
\begin{itemize}
\item $Q_G$ = Carga total que se debe entregar al \textsl{gate} del MOS.
\item $Q_{RR}$ = Carga entregada al diodo en inversa durante el tiempo de recuperación (cuando pasa de modo conducción a inversa).
\item $I_{DR}$ = Corriente de fuga del diodo en inversa.
\item $I_{GS}$ = Corriente que circula por la resistencia de \textsl{gate-source}.
\item $f_{PWM}$ = frecuencia de conmutación.
\end{itemize}

\noindent Por lo tanto, al reemplazar la ecuación \ref{eq_carga-cap-bootstrap} en la \ref{eq_carga-cap-bootstrap2} resulta:

\begin{equation} \label{eq_cap-bootstrap}
C_{BS} > \frac{Q_G+Q_{RR} + \frac{I_{DR}+I_{GS}}{f_{PWM}}}{\Delta V_{BS}}
\end{equation}

\noindent Según la hoja de datos \cite{IPB160N04} del MOSFET IPB160N04, se obtiene que $Q_G= 170\:nC$. Por lo tanto, al adoptar una caída de tensión tolerable en el capacitor de $\Delta V_{BS} = 0.1\:V$, es posible dimensionarlo para que posea carga suficiente para mantener al MOSFET siempre encendido.

\noindent Para el cálculo de la carga de recuperación $Q_{RR}$ se puede considerar que la forma de onda de la corriente de recuperación es triangular. De esta forma,  $Q_{RR}$ es aproximadamente igual a la mitad del producto entre el pico de la magnitud de corriente inversa y la duración del tiempo de recuperación.  Debido a que se usa el diodo RSX205LAM30TR se obtiene, a partir de \cite{RSX205LAM30}, que  $I_R$ es igual a $0.1\:A$  y  el tiempo de recuperación de inversión es de $12.5\:ns$. Por lo tanto, la carga de recuperación resulta de $0.625\:nC$. Además, la corriente inversa de fuga del diodo de \textsl{bootstrap} tiene un valor de $I_{DR} =2 \:mA\:(@\: T=75^{\circ}\:C, V_R= 24\:V)$.

\noindent La corriente $I_{GS}$ tiene forma exponencial pero se aproxima a una constante debido a que el intervalo de tiempo es pequeño. Por lo tanto, puede calcularse como la diferencia de tensión del capacitor de \textsl{bootstrap} ($V_B=12\:V$) dividido el valor de la resistencia \textsl{gate-source}, que es de $4.7\:k\Omega$. Por lo tanto, $I_{GS}=2.55 \:mA$. 

\noindent Debido a que el controlador por histéresis no asegura que haya una conmutación en un tiempo constante (como se observa en la figura \ref{fig:img_respuesta-al-escalon}), se decidió superponer una conmutación auxiliar de $50\:kHz$ (como se explica en el apartado \ref{secc_conmutacion-auxiliar}), lo que resulta en $f_{PWM}=50 \:kHz$. 

\noindent Al reemplazar los valores obtenidos en \ref{eq_cap-bootstrap}, se obtiene:

\begin{equation} 
	\begin{aligned}
		C_{BS} &> \frac{170 \:nC + 0.625\:nC + \frac{2 \:mA + 2.55 \:mA}{50 \:kHz}}{0.1 \:V}\\
	\end{aligned}
\end{equation}

\begin{equation} 
	\begin{aligned}
		C_{BS} &> 2.61 \:\mu F\\	
	\end{aligned}
\end{equation}

\noindent Por lo tanto, una capacidad mayor a $2.61 \:\mu F$ resulta en una caída menor a $0.1\:V$ en el capacitor de \textsl{bootstrap} durante el tiempo de encendido de los MOSFET. Podría usarse un capacitor más pequeño, a costa de permitir una mayor caída de tensión en el capacitor. 

\noindent Finalmente, se decidió utilizar dos capacitores de \textsl{bootstrap} en paralelo de $5.6 \:\mu F$ cada uno, con el objetivo de reducir la resistencia serie.

\subsection{Resistencia entre \textsl{gate} y \textsl{source}} \label{secc_res_gate_source}

\noindent Se colocan resistencias que conectan el \textsl{gate} y el \textsl{source} de cada MOS en el puente H. Estas se observan en la figura \ref{fig:img_capacitores-puenteH} como $R_1$, $R_2$, $R_3$ y $R_4$. Su propósito es evitar que el \textsl{gate} del MOSFET se encuentre cargado cuando el circuito se enciende y el \textsl{driver} de corriente aún no puede descargarlo. Además, ayuda a evitar que se encienda el MOSFET por ruido acoplado capacitivamente. 

\noindent Se utiliza una resistencia de $4.7 \:k\Omega$ debido a que permite que el \textsl{gate} se descargue en un tiempo rápido, consumiendo solo $2.55\:mA$ del capacitor de \textsl{bootstrap}.

\subsection{Protección del \textsl{gate}}

\noindent El \textsl{gate} de los MOS es sensible a las sobretensiones. Soporta como máximo $\pm 20\:V$. Una descarga electrostática (ESD) puede sobrepasar ampliamente este valor de tensión y dañar el MOS al acercar la mano o la sonda del osciloscopio. Para protegerlo se coloca un diodo TVS entre el \textsl{gate} y \textsl{source} de cada transistor, de manera de limitar la tensión que se desarrolla en el \textsl{gate} a un valor seguro.

\noindent Se eligen los TVS SMAJ15 con una tensión bidireccional de $\pm 15\:V$.

\subsection{Tiempo muerto}

\noindent Para evitar generar un cortocircuito durante la conmutación de los transistores, el \textsl{driver} HIP4081A permite configurar un tiempo muerto que debe transcurrir desde que se apaga un transistor y se enciende el próximo. Esto se configura mediante dos resistencias conectadas a sus pines LDEL y HDEL.

\noindent Para saber el tiempo muerto necesario, debe conocerse el tiempo que tarda en apagarse un MOSFET IPB160N04. De \cite{IPB160N04} se obtiene que este tiempo es de $63\:ns$ (teniendo en cuenta el $T_{OFF}$ y el $T_{FALL}$). Por lo tanto, al considerar que esta aplicación espcífica no requiere un tiempo de encendido rápido de los MOSFET, se elige que el tiempo muerto sea de $100\:ns$.

\noindent Según la hoja de datos del HIP4081A, para obtener ese tiempo muerto, las resistencias en HDEL y LDEL deben ser $200\:k\Omega$.

\subsection{Dimensionamiento de los capacitores de fuente}
	
\noindent Para reducir el consumo de potencia de la red se utilizan capacitores en paralelo a la fuente de $+24\:V$. Esto permite que, una vez que la fuente cargó inicialmente el inductor, en las conmutaciones sucesivas la carga del inductor pase a dichos capacitores en un semiciclo y viceversa en el otro ciclo de conmutación. Idealmente, esta transferencia de energía no tiene pérdidas. Por lo tanto, el consumo de potencia queda reducido a la perdida por disipación de los MOSFET y los demás componentes del controlador de corriente. 

\noindent Estos capacitores deben tener una baja resistencia equivalente serie (ESR) ya que, de lo contrario, disiparían mucha potencia en forma de calor y se acortaría su vida útil. Además generan ripple en la tensión $V_{BUS}$.

\noindent En la figura \ref{fig:img_capacitores-puenteH} los capacitores de la fuente están representados por $C_1$ y $C_2$. Para poder dimensionarlos correctamente hay que tener en cuenta que la forma de onda de la corriente que circula por el electroimán en régimen permanente es aproximadamente triangular. Esta corriente es conducida durante medio ciclo desde estos capacitores hacia el electroimán por $Q_1$ y $Q_4$. Luego, durante la otra mitad del ciclo, la corriente regresa a estos capacitores a través de $Q_2$ y $Q_3$. Esto provoca que la corriente en los capacitores sea, durante el semiciclo encendido, igual al valor medio de la corriente del electroimán, con $ \pm \frac{\Delta I_L}{2}$. Similarmente ocurre en el semiciclo apagado, pero con valor medio $-<I_L>$.  Por lo tanto,  la corriente tiene la forma que se muestra en la figura \ref{fig:img_ccorriente-capacitores}

\begin{figure}[H]
	\centering
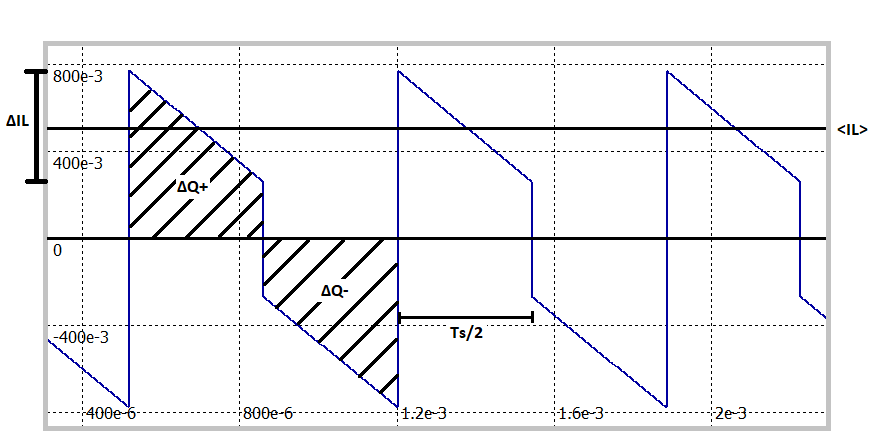
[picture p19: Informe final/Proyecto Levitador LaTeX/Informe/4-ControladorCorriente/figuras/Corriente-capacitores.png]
	
	\caption{Forma de onda de la corriente en $C_1$ y $C_2$.}
	\label{fig:img_ccorriente-capacitores}
\end{figure}

\noindent Por el electroimán circula una corriente media de aproximadamente $21\:A$ en condiciones normales de trabajo. Por lo tanto, la carga del capacitor se puede calcular como:

\begin{equation} 
	\begin{aligned}
   	\Delta Q &= \int I dt\\	
	\end{aligned}
\end{equation}

\begin{equation} 
	\begin{aligned}
		\Delta Q ^+ &= \frac{T_S}{2}*\Delta I_L * \frac{1}{2} + (<I_L> -\frac{\Delta I_L}{2})*\frac{T_S}{2}\\
	\end{aligned}
\end{equation}

\begin{equation} 
	\begin{aligned}
		\Delta Q ^+ &= <I_L> *\frac{T_S}{2}\\
	\end{aligned}
\end{equation}

\noindent Con $\Delta I_L=500 \:mA$ y $T=0.47\:ms$ que corresponde a $Y_g = 2 \:mm$ según la tabla \ref{tab_mediciones}.

\begin{equation} 
\Delta Q = 21\:A * \frac{0.47\:ms}{2} \approx 5\:mC
\end{equation}

\noindent Al considerar que un ripple de $\Delta V=500 \:mV$ es aceptable, se obtiene un valor de:

\begin{equation} 
	c = \frac{\Delta Q}{\Delta V} = 10 \:mF
\end{equation}

\noindent Dado que por los capacitores circula una corriente elevada ($21.25 A$) es recomendable disminuir la ESR total para minimizar la potencia disipada. Por lo tanto, se colocan capacitores en paralelo de baja ESR, como se muestra en la figura \ref{fig:img_capacitores-fuente}.

\begin{figure}[H]
	\centering
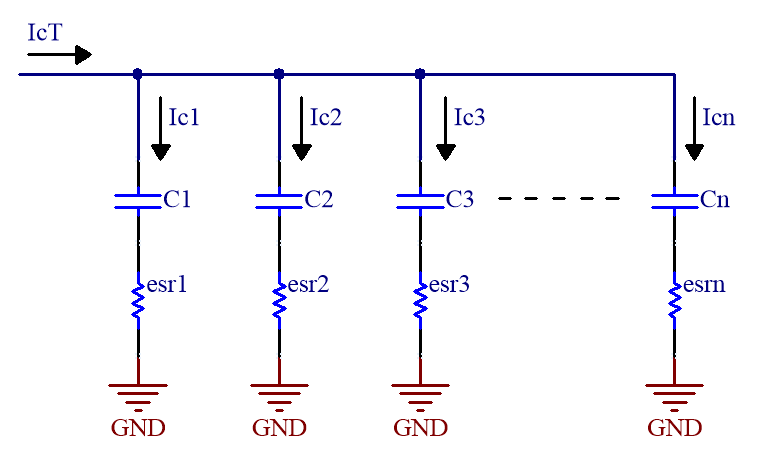
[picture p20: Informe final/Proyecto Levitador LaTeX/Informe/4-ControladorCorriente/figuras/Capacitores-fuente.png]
	
	\caption{Capacitores de la fuente.}
	\label{fig:img_capacitores-fuente}
\end{figure}

\begin{equation} 
	C = C1 + C2 + ... + C_n
\end{equation}

\noindent Si todos los valores de ESR son iguales se obtiene:

\begin{equation} 
R_T = \frac{R_{ESR}}{n}
\end{equation}

\noindent Por lo tanto, se puede calcular la potencia que disipan como:

\begin{equation}\label{eq_potencia} 
	P = I^2 * R_T = 21.25^2 * \frac{R_{ESR}}{n}
\end{equation}

\noindent Se decidió utilizar 6 capacitores  de $2200 \:uF$ con un rating de tensión de $50\:V$ y una ESR de $17 \:\Omega$ (datos obtenidos de \cite{EKY-350ELL222MM25S}) . De esta forma, al reemplazar en la ecuación \ref{eq_potencia} se obtiene que la potencia disipada es de: 

\begin{equation} 
	P=1.28\:W
\end{equation}

\subsection{Conmutación de alta frecuencia para el \textsl{bootstrap}}
\label{secc_conmutacion-auxiliar}

\noindent Cuando el MOSFET \textsl{driver} recibe una entrada que activa un MOS del lado superior, este comienza a cargar el \textsl{gate} con ayuda de la tensión que brinda el capacitor de \textsl{bootstrap} asociado a ese MOS. El capacitor de \textsl{bootstrap} entrega energía durante la carga del \textsl{gate} y durante todo el tiempo que el MOS esté activo (debido a la resistencia $R_{GS}$). Para poder recargar el capacitor, debe esperarse a que el \textsl{driver} reciba la entrada necesaria para apagar el MOS. Debido a que la implementación del \textsl{driver} de corriente utiliza un controlador por histéresis, no es posible asegurar que haya una conmutación en un periodo regular.

\noindent Para poder asegurar un periodo de conmutación constante y conocido se agrega un bloque que superpone una conmutación de alta frecuencia a la señal de control que ingresa al MOSFET \textsl{driver}. De esta manera se producen conmutaciones en un intervalo regular que permiten la carga de los capacitores de \textsl{bootstrap}. 

\noindent Se adopta una frecuencia de conmutación auxiliar de $50\:kHz$ y se hace variar el ciclo de trabajo de la salida del comparador con histéresis entre dos valores. Para la carga del inductor se definió que el ciclo de trabajo sea del 90\% mientras que para la descarga sea del 10\%.

\noindent Para generar esta conmutación se agrega el oscilador que se observa en la figura \ref{fig:img_frecuencia-auxiliar} a la salida del comparador con histéresis. La frecuencia de conmutación se puede obtener en función de $C_1$ como:

\begin{equation} 
	F_{aux} = \frac{4.5*10^{-5}}{C1} [Hz]
\end{equation}

\noindent Esta frecuencia debe ser mucho mayor a la fundamental de la corriente triangular para evitar problemas en el funcionamiento del sistema y, además, debe ser lo suficientemente alta para poder ser filtrada sin inconvenientes en la etapa de estimación de posición (como se explica en el capítulo \ref{cap:Estimador Analogico}). Por lo tanto, al adoptar una frecuencia auxiliar de $50\:kHz$, resulta en $C_1= 900\:pF$.

\begin{figure}[H]
	\centering
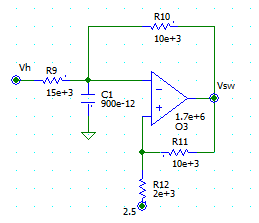
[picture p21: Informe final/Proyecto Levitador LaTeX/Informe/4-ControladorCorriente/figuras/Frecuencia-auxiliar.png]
	
	\caption{Circuito oscilador de frecuencia auxiliar.}
	\label{fig:img_frecuencia-auxiliar}
\end{figure}

\subsection{Simulación del sistema con oscilador auxiliar}

\noindent En la figura \ref{fig:img_corriente-auxiliar} se muestran las formas de onda obtenidas con el oscilador auxiliar utilizado para el correcto funcionamiento del \textsl{bootstrap}. 

\begin{figure}[H]
	\centering
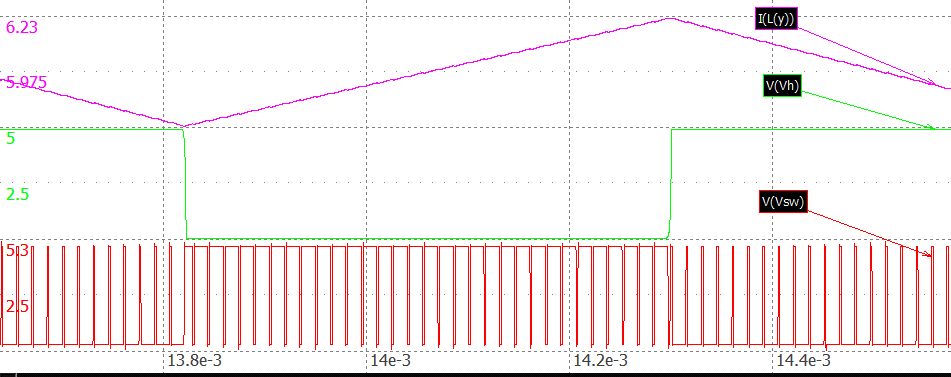
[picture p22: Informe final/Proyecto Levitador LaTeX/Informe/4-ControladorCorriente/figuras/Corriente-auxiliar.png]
	
	\caption{Simulación de corriente en el electroimán, salida del comparador, y conmutación auxiliar.}
	\label{fig:img_corriente-auxiliar}
\end{figure}

\section{Criterio de utilización de la topología de puente H}
\label{secc_justificación-puente-H}

\noindent Es necesario que el controlador presente una corriente media unidireccional, ya que una corriente media negativa es indistinguible de la positiva puesto que tiene el mismo efecto en la fuerza del electroimán, pero el signo del controlador hace inestable el lazo de control. Sin embargo, puede darse el caso que la corriente en el electroimán sea negativa de manera instantánea con valor medio positivo. En ese caso, es necesario que se conserve la forma de onda triangular ya que de lo contrario traería problemas en la estimación de la posición (como se explica en el capítulo \ref{cap:Estimador Analogico}). Por lo tanto, para evitar que la misma sea recortada, es necesario que el controlador permita excursiones negativas sin perder la forma de onda. Esta situación puede darse en los siguientes casos:

\begin{itemize} 
	\item Cuando el sistema arranca desde corriente cero, hasta que el valor medio de corriente supera la mitad del ripple de corriente $(\Delta I_{L})$.
	
	\item Cuando el entrehierro es pequeño y se trabaja con peso reducido la corriente media puede llegar a ser menor que el ripple $\Delta I_{L}$.
\end{itemize}

\noindent Por estos motivos se debe utilizar una topología de puente completo, puesto que permite la excursión negativa de la corriente mientras que mantiene en funcionamiento al estimador de posición.

\subsection{Ajuste para evitar lazo abierto con corriente instantánea negativa}

\noindent El sensor de efecto Hall entrega una tensión proporcional a la corriente que circula por el electroimán con un \textsl{offset} de $2.5\:V$. Es decir, para corrientes positivas, la salida será mayor a $2.5\:V$, y para corrientes negativas, menor.

\noindent La salida de este sensor se realimenta hacia la entrada del controlador de corriente mediante un operacional, quitándole el \textsl{offset} de $2.5\:V$. Debido a que se utiliza una fuente simple para la alimentación, el circuito encargado de realimentar solo permite excursiones positivas de la corriente mientras que las negativas son recortadas. Esto presenta un problema ya que si ocurre el caso de que la corriente del electroimán se haga negativa instantáneamente, la tensión de salida del sensor de efecto Hall será menor a $2.5\:V$, por lo que la salida del operacional será recortada y, por lo tanto, el sistema quedará a lazo abierto.

\noindent Para solucionar este problema se analizaron dos alternativas:

\begin{itemize} 
	\item Elevar el \textsl{set-point} del sensor de efecto Hall.
	
	\item Utilizar una alimentación bipolar para el operacional de realimentación.
\end{itemize}

\noindent Entre estas se eligió la primer alternativa, ya que se puede implementar con mayor facilidad en el circuito. Hay que tener en cuenta que, al incrementar el \textsl{offset} del sensor, también se debe incrementar en la misma proporción la tensión de referencia de la etapa de entrada al controlador de corriente.

\noindent Para saber qué valor utilizar para el \textsl{offset} se debe calcular el mínimo de tensión entregada por el sensor de efecto Hall. Esto se da cuando la referencia del controlador de corriente es de $0\:V$, con lo cual la corriente media del electroimán será $0 \:A$ con una excursión de $±250\:mA$. Lo que significa una tensión de salida del sensor de efecto Hall de $13.3\:mV$ por encima y debajo del \textsl{offset}. Para tomar un margen se incrementa el \textsl{offset} a $2.6\:V$. 

\section{Características estáticas y dinámicas del controlador}

\subsection{Corriente media del electroimán}

\noindent Para saber la corriente media que hay a la salida al aplicarle cierta tensión en la entrada, se utiliza la transferencia de lazo cerrado (sin considerar polos, y suponiendo alta ganancia de lazo abierto):

\begin{equation} 
	I_L = V_{iLRef} * \frac{K_{in}}{H(s)} = V_{iLRef} * 6 \frac{A}{V}
\end{equation}

\subsection{Frecuencia de conmutación de la corriente}

\noindent La frecuencia de conmutación del sistema se obtiene con:

\begin{equation}\label{eq_frec-sw} 
f_{SW} = \frac{V_{BUS}}{2*\Delta I_L * L(Y_g)}
\end{equation}

\noindent Para $Y_g = 4 \:mm $ se tiene una inductancia $L(4\:mm) = 16.44 \:mHy$ , lo cual resulta en una frecuencia $f_{SW }= 1460 \:Hz$ .

\subsection{Ancho de banda del controlador}\label{esccion_AB_Controlador} 

\noindent La dinámica del controlador, al depender de la inductancia, lo hace también del entrehierro. El ancho de banda (o velocidad con que responde) está limitado por la constante de tiempo del inductor con su resistencia serie. Juntas forman un sistema lineal de primer orden, con un polo en: 

\begin{equation} \label{eq_frec-angular}
	\omega _{polo} = \frac{R_L}{L(Y_g)}
\end{equation}

\noindent Al tomar las condiciones del problema en el punto de linealización con $Y_{0}=4\:mm$, resulta una inductancia $L = 7.55 \:mHy + 8.89 \:mHy$. Luego, al considerar la resistencia del bobinado $R_L=0.2\:\Omega$, se calcula la ubicación del polo:

\begin{equation} 
	\omega _{polo} = \frac{0.2\:\Omega}{16.44 \:mHy} = 12.17 \:rad/s
\end{equation}

\noindent La tabla \ref{tab_mediciones} muestra  entre qué valores de frecuencia se ve afectada la forma de onda al modificarse la distancia de separación.

\begin{equation} \label{eq_DeltaT}
	\Delta T [s] = \frac{\Delta I_L * (L(Y_g) + L_{\infty})}{V_{BUS}}
\end{equation}

\noindent En la ecuación \ref{eq_DeltaT}, $\Delta T$ representa el tiempo de crecimiento o de decrecimiento de la rampa de corriente (sin considerar la resistencia del bobinado) en torno al valor nominal. El doble de este tiempo es igual al periodo de la corriente triangular $(2*T=\frac{1}{F_{SW}})$.

\noindent Según las mediciones de inductancia realizadas y, al aplicar las ecuaciones \ref{eq_frec-sw}, \ref{eq_frec-angular} y \ref{eq_DeltaT}, se obtuvo la tabla \ref{tab_mediciones}.

\begin{table}[H]
	\begin{center}
		\begin{tabular}{| c | c | c | c | c |}
			\hline
			$Y_g\:[mm]$ & $L(Y_g)\:[mHy]$ & $\Delta T\:[ms]$ & $f_{SW}\:[Hz]$ & $\omega _{polo}\:[rad/s]$\\ \hline
			0 & 76.45 & 1.59 & 313.93 & 2.62\\ \hline
			1 & 33.42 & 0.70 & 718.13 & 5.98\\ \hline
			2 & 22.64 &	0.47 & 1060.07 & 8.83\\ \hline
			3 &	18.8 & 0.39 & 1276.60 & 10.64\\ \hline
			4.4 & 15.5 & 0.32 & 1548.39 & 12.90\\ \hline
			5.2 & 14.7 & 0.31 & 1632.65 & 13.61\\ \hline
			6.5 & 14.4 & 0.30 & 1666.67 & 13.89\\ \hline
			8.23 & 12.4 & 0.26 & 1935.48 & 16.13\\ \hline
			$\infty$ & 8.89 & 0.19 & 2699.66 & 22.5	\\ \hline
		\end{tabular}
		\caption{Valores calculados y medidos en función del entrehierro.}
		\label{tab_mediciones}
	\end{center}
\end{table}

\subsection{Transferencia lineal del controlador de corriente}

\noindent En la ecuación \ref{eq_TLC-cc} se muestra la transferencia linealizada del controlador de corriente para una distancia de separación de $Y_{0}=4\:mm$.

\begin{equation} \label{eq_TLC-cc}
G_{iL}(s) = \frac{6}{1+\frac{s}{12.17}}
\end{equation}

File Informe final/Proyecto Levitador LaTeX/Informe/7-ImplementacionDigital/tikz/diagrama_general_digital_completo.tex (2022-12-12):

\tikzset{%
	buffer/.style={
		draw,
		shape border rotate=270,
		regular polygon,
		regular polygon sides=3,
		fill=blue!20,
		node distance=2cm,
		minimum height=4em
	}
}

\tikzstyle{block} = [draw, fill=blue!20, rectangle, 
minimum height=2.5em, minimum width=3em]

%Acá se define eñ diagrama en bloques completo
\begin{tikzpicture}[auto, node distance=1.5cm,>=latex']
	% We start by placing the blocks
	\node [input, name=input] {};
	\node [buffer, right=of input](F){F};
	\node [sum, right of=F, node distance=1.5cm] (suma_externa) {+};
	\node [block, right=of suma_externa] (externo) {$G_{ext}(z)$};
	\node [sum, right=2cm of externo] (suma_interna) {+};
	\node[block, right=of suma_interna] (interno) {$G_c(z)$};
	%\node [block, right=of interno] (gil) {$G_{IL}(w)$};
	\node [block, right=of interno] (planta) {$G_T(s)$};
	\node [coordinate, below=of interno] (realimentacion_interna) {$H_{estim}(w)$};
	
	\node [coordinate, below=2cm of externo] (realimentacion_externa) {$H_{estim}$};
%	
%	\node [block, right of=suma] (amplificador) {$A(s)$};
	\node [output, right of=planta, node distance=3cm] (output) {};
%	\node [block, below of=amplificador] (realimentacion) {$H(s)$};
%	
%	
%	% Once the nodes are placed, connecting them is easy. 
	\draw [draw,->] (input) -- node[pos=0.2]{$Y_{ref}$} (F);
	\draw [draw,->] (F) -- node[pos=0.9]{$+$}(suma_externa);
	\draw [draw,->] (suma_externa) -- node{$Ve_{ext}$} (externo);
	\draw [draw,->] (externo) -- node{$V_{ref_c}$} node[pos=0.95]{$+$} (suma_interna);
	\draw [draw,->] (suma_interna) -- node{$Ve_{int}$}(interno);
	\draw [draw,->] (interno) -- node{$V_{IL_{ref}}$} (planta);
	%\draw [draw,->] (gil) -- (planta);
	\draw [draw,->] (planta) -- node[name=y]{$Y_g$} (output);
%	\draw [draw,->] (amplificador) -- node[name=y]{$V_{deriv}$} (output);
	\draw [-] (y) |- (realimentacion_interna);
	\draw [->] (realimentacion_interna) -|  node[pos=0.99]{$+$} (suma_interna);
	\draw [-] (y) |- (realimentacion_externa);
	\draw [->] (realimentacion_externa) -|  node[pos=0.99]{$+$} (suma_externa);
\end{tikzpicture}

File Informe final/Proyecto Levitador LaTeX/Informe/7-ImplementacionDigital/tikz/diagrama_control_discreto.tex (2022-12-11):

\tikzset{%
	buffer/.style={
		draw,
		shape border rotate=270,
		regular polygon,
		regular polygon sides=3,
		fill=blue!20,
		node distance=2cm,
		minimum height=4em
	}
}

\tikzstyle{block} = [draw, fill=blue!20, rectangle, 
minimum height=2.5em, minimum width=3em]

%Acá se define eñ diagrama en bloques completo
\begin{tikzpicture}[auto, node distance=1cm,>=latex']
	% We start by placing the blocks
	\node [input, name=input] {R(z)};
	\node [sum, right of=input, node distance=1.5cm] (suma_externa) {+};
	\node [block, right=of suma_externa] (compensador) {$D(z)$};
	\node[block, right=of compensador] (dac) {DAC};
	%\node [block, right=of interno] (gil) {$G_{IL}(w)$};
	\node [block, right=of dac] (planta) {$G(s)$};
	\node [block, below=of dac] (realimentacion) {ADC};
	
	\node [output, right of=planta, node distance=3cm] (output) {};

%	% Once the nodes are placed, connecting them is easy. 
	\draw [draw,->] (input) -- node[pos=0.2]{$R(z)$} node[pos=0.9]{$+$}(suma_externa);
	\draw [draw,->] (suma_externa) -- node{$E(z)$} (compensador);
	\draw [draw,->] (compensador) -- node{$U(z)$} (dac);
	\draw [draw,->] (dac) -- node{$U(s)$} (planta);
	%\draw [draw,->] (gil) -- (planta);
	\draw [draw,->] (planta) -- node[name=y]{$C(s)$} (output);
%	\draw [draw,->] (amplificador) -- node[name=y]{$V_{deriv}$} (output);
	\draw [-] (y) |- (realimentacion);
	\draw [->] (realimentacion) -| node[pos=0.25]{$C(z)$} node[pos=0.99]{$-$} (suma_externa);
\end{tikzpicture}

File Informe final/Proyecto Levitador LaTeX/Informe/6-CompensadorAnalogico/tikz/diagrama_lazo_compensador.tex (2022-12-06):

\tikzset{%
	buffer/.style={
		draw,
		shape border rotate=270,
		regular polygon,
		regular polygon sides=3,
		fill=blue!20,
		node distance=2cm,
		minimum height=4em
	}
}

\tikzstyle{block} = [draw, fill=blue!20, rectangle, 
minimum height=2.5em, minimum width=3em]

%Acá se define eñ diagrama en bloques completo
\begin{tikzpicture}[auto, node distance=2.5cm,>=latex']
	% We start by placing the blocks
	\node [input, name=input] {};
	\node [block, right=of input](F){$G^-$};
	\node [sum, right of=F, node distance=2cm] (suma_interna) {+};
	\node [block, right=of suma_interna] (interno) {$A_{w}$};
	%\node [block, right=of interno] (tlc_interna) {$TLC_{interna}$};
	\node [block, below= 1cm of interno, node distance=0.5cm] (realimentacion_interna) {$H$};

%	\node [block, right of=suma] (amplificador) {$A(s)$};
	\node [output, right of=tlc_interna, node distance=3cm] (output) {};
%	\node [block, below of=amplificador] (realimentacion) {$H(s)$};
%	
%	
%	% Once the nodes are placed, connecting them is easy. 
	\draw [draw,->] (input) -- node[pos=0.2]{$Vaf_{in}$} (F);
	\draw [draw,->] (F) --  node[pos=0.9]{$+$}(suma_interna);
	\draw [draw,->] (suma_interna) -- node{$V_d$} (interno);
	%\draw [draw,->] (interno) -- node{$V_{ref_c}$} (tlc_interna);
	\draw [draw,->] (interno) -- node[name=y]{$Vaf_{out}$} (output);
%	\draw [draw,->] (amplificador) -- node[name=y]{$V_{deriv}$} (output);
	\draw [->] (y) |- (realimentacion_interna);
	\draw [->] (realimentacion_interna) -| node[pos=0.25]{}  node[pos=0.99]{$-$} (suma_interna);
%	\draw [->] (y) |- (realimentacion_externa);
%	\draw [->] (realimentacion_externa) -| node[pos=0.25]{$V_{estim}$} node[pos=0.99]{-} (suma_externa);
\end{tikzpicture}

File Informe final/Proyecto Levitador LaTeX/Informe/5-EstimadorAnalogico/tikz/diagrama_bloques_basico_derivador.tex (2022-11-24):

%Acá se define eñ diagrama en bloques completo
\begin{tikzpicture}[auto, node distance=2.5cm,>=latex']
	% We start by placing the blocks
	\node [input, name=input] {};
	\node [block, right of=input] (derivador) {$DERIVADOR$};

	\node [block, right of=derivador, 
	node distance=5.5cm] (modulo) {$RECTIFICADOR$};
	\node [output, right of=modulo, node distance=3.5cm] (output) {};

	% Once the nodes are placed, connecting them is easy. 
	\draw [draw,->] (input) -- node[pos=0.1]{$V_{IL_{feed}}$} (derivador);
	\draw [draw,->] (derivador) -- node{$V_{deriv}$} (modulo);
	\draw [->] (modulo) -- node [name=y] {$V_{estim}$}(output);
\end{tikzpicture}

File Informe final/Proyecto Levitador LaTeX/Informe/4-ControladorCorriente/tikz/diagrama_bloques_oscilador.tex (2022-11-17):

%importo el bloque de histeresis que definí en otro archivo
\input{tikz/histeresis.tex}

\tikzset{%
	buffer/.style={
		draw,
		shape border rotate=270,
		regular polygon,
		regular polygon sides=3,
		fill=blue!20,
		node distance=2cm,
		minimum height=4em
	}
}

%Acá se define eñ diagrama en bloques completo
\begin{tikzpicture}[auto, node distance=2.5cm,>=latex']
% We start by placing the blocks
\node [input, name=input] {};
\node [block, right of=input] (Kin) {$K_{in}$};
\node [sum, right of=Kin, node distance=2cm] (sum) {};
\node [block, right of=sum] (controller) {\histvh};
\node [draw,circle, fill=blue!20, right of=controller](multiplier){X};
\node [coordinate, above of=multiplier, node distance=1cm](osc) {}; 
\node [buffer, right of=multiplier, node distance=2cm](buffer){};
\node [coordinate, above of=buffer, node distance=1cm](Vcc){};
\node [coordinate, below of=buffer, node distance=1cm](Vee){};
\node [block, right of=buffer, 
node distance=3.5cm] (system) {${\displaystyle\frac{1}{s*L(Y_g)+R_L}}$};
% We draw an edge between the controller and system block to 
% calculate the coordinate u. We need it to place the measurement block. 
\draw [->] (controller) -- node[name=u]{$V_h$} (multiplier);
\draw [->] (multiplier) -- node{$V_{sw}$}(buffer);
\draw [->] (osc) -| node{$F_{aux}$} (multiplier);
\draw (Vcc) -| node{$V_{cc}$} (buffer);
\draw (Vee) -| node[right]{$-V_{cc}$} (buffer);
\draw [->] (buffer) -- node {$V_L$} (system);
\node [output, right of=system] (output) {};
\node [block, below of=u, node distance=3cm] (measurements) {H(s)};

% Once the nodes are placed, connecting them is easy. 
\draw [draw,->] (input) -- node[pos=0.1]{$V_{IL_{ref}}$} (Kin);
\draw [draw,->] (Kin) -- node[pos=0.9]{$+$} (sum);
\draw [->] (sum) -- node {$e$} (controller);
\draw [->] (system) -- node [name=y] {$I_L$}(output);
\draw  (y) |- (measurements);
\draw [->] (measurements) -| node[pos=0.99] {$-$} node[above, pos=0.9, right] {$V_{IL_{feed}}$} (sum); %node [near end] {$I_{L_{feed}}$} 
\end{tikzpicture}

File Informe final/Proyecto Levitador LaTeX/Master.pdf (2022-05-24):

# MODELO DE LEVITADOR

# MAGNETICO EXPERIMENTAL

´

# PARA PRACTICA DOCENTE

´

## Juan Manuel Guariste

## Ignacio Islas

## Javier Mosconi

Este Trabajo Final de carrera fue presentado al Departamento de Electrónica y

Computación de la Facultad de Ingeniería de la Universidad Nacional de

Mar del Plata el día X de Mayo del año 2022, como requisito parcial para

la obtención del título de

### Ingeniero en Electrónica

### Director: Ing. Walter Kloster

### Co-Director: Ing. Gustavo Uicich

El presente trabajo fue realizado en el Laboratorio de Instrumentación y

Control del Departamento de Electrónica y Computación, ICyTE, Facultad de

Ingeniería, Universidad Nacional de Mar del Plata.

MODIFICARRRRRRRR LUEGO EN MASTER.tex

iv

´

# Indice general

Índice de tablas | IX
Índice de figuras | XI
1. Introduccion | 1
2. Caracterización del Electroimán | 7
3. Controlador de corriente | 19

v

3.1.2.2. Simulación de un escalón en la referencia de co-
3.1.2.4. Dimensionamiento de capacitor de bootstrap . . . | 29
3.1.2.4.1.Resistencia entre gate y source . . . . | 33
3.1.2.5. Dimensionamiento de los capacitores de fuente . . | 34
3.1.2.6. Conmutación de alta frecuencia para el bootstrap | 37
3.1.2.7. Simulación del sistema con oscilador auxiliar . . . | 39
3.1.3. Características estáticas y dinámicas del controlador . . . | 40
3.1.3.2. Frecuencia de conmutación de la corriente . . . . | 40
4. EstimadorAnalogico | 43

vi

5. Compensador Analogico | 67
5.1.3.3. Implementación circuital del bloque de ganancia
6. Implementacion Digital | 75

vii

7. PCB | 107
8. Bibliografía | 109

viii

´

# Indice de tablas

3.1. Valores calculados y medidos en función del Gap de aire | | 42
4.1. Vyf en función de la posición | | 48
4.2. Resultados de simulación del estimador | | 64
5.1. Tensión de referencia [Vin] Vs separación deseada [Y] | | 72
6.1. Valores de frecuencia calculados a partir de las mediciones de in-
ductancia realizadas | 77

ix

x

´

# Indice de figuras

1.1. Esquema del producto | | 3
1.2. Diagrama en bloques del sistema | | 4
2.1. Dimensiones del electroimán | | 8
2.2. Carrete de plástico para el bobinado | | 9
2.3. Modelado físico | | 10
2.4. Toroide con gap de aire | | 12
3.1. Diagrama en bloques simplificado del controlador de corriente. . . | 20
3.2. Etapa de entrada | | 21
3.3. Comparador con histéresis | | 22
3.4. Puente H y sensor de efecto Hall | | 23
3.5. Resta del Vbias al sensor de efecto Hall | | 23
3.6. Formas de onda de corriente en el electroimán y salida del compa-
rador | | 24
3.7. Respuesta al escalón del circuito | | 25
3.8. Topología elemental del puente H | | 26
3.9. Configuración Bootstrap simplificada | | 28
3.10. Puente H | | 30
3.11. Forma de onda de la corriente en C1 y C2 | | 35

xi

3.12. Capacitores de la fuente | | 36
3.13. Circuito oscilador de frecuencia auxiliar | | 39
3.14. Simulación de corriente en el electroimán, salida del comparador,
y conmutación auxiliar | | 39
4.1. Diagrama en Bloques del Estimador | | 44
4.2. Circuito del electroimán con el driver de corriente | | 45
4.3. Circuito derivador | | 46
4.4. Circuito derivador compensado | | 48
4.5. GH del derivador compensado.png | | 49
4.6. Transferencia de lazo cerrado | | 50
4.7. Filtro para la entrada del derivador | | 51
4.8. Respuesta en frecuencia del filtro activo | | 52
4.9. Forma de onda luego de rectificar sin compensación IR | | 53
4.10. Esquema circuital del derivador | | 54
4.11. Generación de Vbias | | 55
4.12. Formas de onda obtenidas en la simulación | | 56
4.13. Rectificador y restador | | 57
4.14. Restador | | 60
4.15. Esquema circuital del restador con una etapa de filtrado en 159,2 Hz. 62
4.16. Circuito estimador de posición completo | | 63
4.17. Simulación final del estimador | | 64
5.1. Diagrama del sistema completo | | 67
5.2. Diseño circuital de una red de adelanto de fase | | 68
5.3. Etapa de ganancia del compensador | | 69
5.4. Implementación circuital del integrador | | 71
5.5. Diagrama en bloques final | | 72

xii

5.6. Etapa de entrada | | 73
6.1. Diagrama en bloques de la implementación digital | | 76
6.2. Diagrama en bloques de la etapa digital simplificado | | 76
6.3. Diagrama de flujo del procesamiento de las muestras adquiridas. . | 79
6.4. Variación de pendiente ante mínimo cambio de posición | | 84
6.5. Circuito acondicionador para componente alterna de corriente del
electroimán | 87
6.6. Circuito acondicionador para componente alterna de corriente del
electroimán. | | | 88
6.7. Circuito acondicionador para componente continua de corriente del
electroimán. | | | 88
6.8. Circuito acondicionador para la salida del DAC correspondiente al
compensador | 89
6.9. Circuito acondicionador para la salida del DAC correspondiente al
estimador digital | | 90
6.10. Diagrama de Bode de lazo abierto GHT con M=30 Kg | | 92
6.11. Diagrama de Nyquist de GHT con M=30 Kg | | 92
6.12. Forma del diagrama de Nyquist deseado | | 93
6.13. Diagrama de Bode de GHT*GC para K=1 y M=30 Kg | | 95
6.14. Diagrama de Bode de GHT*GC para K=2630 y M=30 Kg | | 96
6.15. Diagrama de Nyquist de GHT*GC para K=2630 y M=30 Kg. . . | 97
6.16. Respuesta al escalón para M=30 Kg | | 98
6.17. Diagrama de Bode de GHT ∗ GC para M=1 Kg | | 99
6.18. Diagrama de Nyquist de GHT ∗ GC para M=1 Kg | | 99
6.19. Respuesta al escalón para M=1 Kg | 100
6.20. Diagrama del sistema completo | 100

xiii

6.21. Lugar de raíces con el integrador | 102
6.22. Respuesta al escalón con integrador con Kint =1 y M=30 Kg. . . 103
6.23. Respuesta al escalón con integrador para Kint =20 y M = 30 Kg. 104
6.24. Respuesta al escalón con integrador para Kint =20 y M = 1 Kg. . 105

xiv

# Agradecimientos

Al DIEGOTE PAPA

xv

# Capítulo 1

# Introduccion

Ver de poner una intro general de levitación magnetica y la importancia de los sistemas de control

El desarrollo de este sistema de levitación magnética surge como idea de los

responsables de la cátedra Sistemas de Control de la carrera de Ingeniería

Electrónica, con el objetivo de disponer de una planta de control para reali-

zar prácticas en clase. Una primera versión de este dispositivo fue desarrollada y

construída por la cátedra. Los integrantes de este proyecto tuvieron la oportuni-

dad de realizarle pruebas y modificaciones durante el cursado de la asignatura.

Sin embargo, no se pudo lograr que el dispositivo funcionara correctamente al

finalizar la cursada. Por este motivo, se propuso hacer un rediseño de todas las

etapas que componen al sistema en el marco de un proyecto final.

## 1.1. Alcance del proyecto

El objetivo de este proyecto es diseñar un sistema de levitación magnética a partir

de un electroimán de laminación normalizada con núcleo tipo “E”. Este sistema

integra las etapas de driver de corriente de potencia, estimación de distancia de

levitación, y control de la planta. Estas dos últimas deben implementarse tanto

1

2

en forma analógica como digital.

Este documento contempla el proceso de diseño y modelado de todas las etapas

pertenecientes al sistema, junto con su implementación circuital y simulaciones.

Además, se realiza el diseño del circuito impreso de la placa de control.

## 1.2. Contexto del proyecto

El proyecto comenzó en junio del 2020. Inicialmente tenía como objetivo el diseño

y la construcción de un prototipo funcional que permitiera a los alumnos de la

asignatura de Sistemas de Control realizar mediciones y observar el comporta-

miento de las distintas etapas que componen el sistema. Sin embargo, debido a

los retrasos ocasionados por la pandemia (COVID-19), los costos asociados a los

componentes y a la fabricación de la placa de control, sumado a la necesidad

de no extender indefinidamente el proyecto, se optó por acotar el alcance sólo al

diseño teórico de todas las etapas y del circuito impreso.

Se espera que en el futuro se pueda construir el sistema de levitación magnética

para que sirva como herramienta para los alumnos, de forma tal que les permita

experimentar y afianzar los conceptos teóricos adquiridos durante el transcurso

de la cursada.

## 1.3. Descripción del dispositivo

El producto está compuesto por dos partes principales: un electroimán y una placa

de control. El electroimán tiene dos piezas formadas por láminas de acero apiladas:

una con forma de “E”, que tiene un cable bobinado en su rama central. y otra con

forma de “I” que es atraída por la primera mediante una fuerza electromagnética.

Esta fuerza es regulada por la placa de control, que mantiene la distancia de

Capítulo 1. Introduccion | 3

separación o “gap” de aire deseado entre ellas mientras el objeto que se desea

hacer levitar se sujeta de la pieza en forma de “I”. El sistema completo se muestra

en la figura 1.1.

Figura 1.1: Esquema del producto.

La fuerza electromagnética es regulada por la placa de control con el objetivo

de mantener fija la distancia Yo, a pesar de las perturbaciones externas que el

sistema pueda recibir.

El sistema solo ejerce control de posición en el eje vertical, por lo tanto no puede

responder ante perturbaciones horizontales sobre el objeto.

El sistema está conformado por los bloques que se muestran en la Figura 1.2.

Se utilizan dos controladores distintos: uno analógico y otro digital. Cada uno

de ellos se compone de un compensador y un estimador de posición. El usuario

4

decidirá cual de estas implementaciones ejercerá el control mediante la utilización

de un switch, por lo que solo una estará activa al mismo tiempo. El sistema

analógico está formado por un conjunto de componentes pasivos y amplificadores

operacionales, mientras que el digital está basado en un microcontrolador re-

programable. Ponerle un signo menos al restador de la figura 1.2

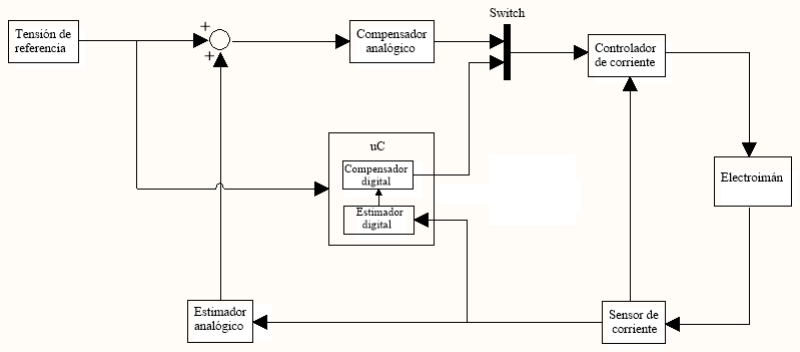
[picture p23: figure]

Figura 1.2: Diagrama en bloques del sistema.

El estimador de posición se encarga de entregar una tensión proporcional al gap

de aire real en función de la corriente que circula por el electroimán. El usuario

puede modificar el gap de aire que desea mediante un potenciómetro presente en

la placa de control. Tanto la implementación analógica como la digital reciben

como entrada esta tensión. Luego, es comparada con la estimación y se utiliza

como entrada para el compensador.

La función del compensador es garantizar la estabilidad del sistema. Esto lo logra

al modificar la referencia del controlador de corriente mediante una acción de

control.

Capítulo 1. Introduccion | 5

Por otro lado, el controlador de corriente se encarga de proveer corriente al elec-

troimán de forma tal que le permita generar la fuerza electromagnética necesaria

para mantener el gap de aire.

6

# Capítulo 2

# Caracterización del Electroimán

Para el desarrollo del proyecto se dispone ya de un electroimán que funcionará

como actuador del sistema. A partir de sus características constructivas, y del

modelo físico y dinámico del problema, se podrán determinar otros parámetros

del sistema de control.

7

8

## 2.1. Diseño del electroimán

Figura 2.1: Dimensiones del electroimán

El electroimán está compuesto por dos piezas: una con forma de “E” y otra con

forma de “I”. Estas se construyen a partir del apilado de láminas de acero al

silicio de 0,5mm de espesor, cuyas dimensiones se muestran en la figura 2.1. El

apilado de las láminas es tal que la rama central de la E tiene sección cuadrada;

lo que maximiza el área mientras que disminuye el perímetro.

Capítulo 2. Caracterización del Electroimán | 9

El bobinado está conformado por 150 vueltas de alambre de cobre esmaltado de

2,5mm de diámetro enrollado alrededor de un carrete de plástico (figura 2.2) que

luego se ubica en la rama central de la pieza E.

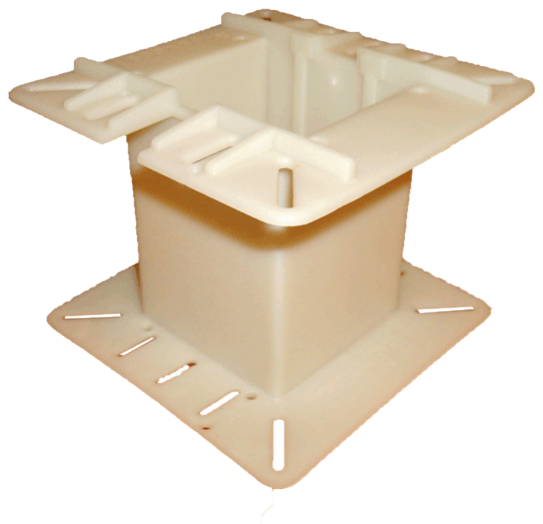
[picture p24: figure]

Figura 2.2: Carrete de plástico para el bobinado

Se utiliza un apilado de láminas cuyo exterior está recubierto por una pintura

esmaltada para aislarlas entre sí con el fin de minimizar las pérdidas de energía

causadas por las corrientes eléctricas que se generan en el núcleo debidas al flujo

10

magnético. . Está construido por una laminación normalizada sin desperdicio 600.

Estas son útiles ya que cada par de laminas E y I puede fabricarse a partir de

una lámina de acero rectangular, de manera de que no se desperdicia material

durante la fabricación. poner figura del electroimán real????

## 2.2. Modelado físico

Se puede modelar el sistema como un objeto de masa puntual que es someti-

do a dos fuerzas opuestas en el eje “Y” de la figura 2.3: la de su propio pe-

so hacia abajo, y una fuerza realizada por el electroimán en sentido contrario.

MARCAR Yo EN LA IMAGEN

Figura 2.3: Modelado físico.

La fuerza correspondiente al peso del objeto es P = m ∗ g, donde m es la masa

en kg y g es la aceleración de la gravedad en m
s

2

. Para mantenerlo levitando en

estado de equilibrio, el electroimán debe generar una fuerza de igual módulo y

sentido contrario. Esto lo logra a partir de la circulación de un flujo magnético

Capítulo 2. Caracterización del Electroimán | 11

entre su núcleo y la pieza con forma de I. Entre estas dos piezas se conforma lo

que se conoce como circuito magnético, en el que la energía fluye impulsada por

una fuerza magnetomotriz.

La fuerza magnetomotriz generada en el núcleo del electroimán es proporcional

a la corriente que circula por su bobinado, y su módulo está dado por la ecua-

ción 2.1, que también la relaciona con la reluctancia del circuito magnético y la

magnitud del flujo magnético.

Fmm = N ∗ i = Rm ∗ ϕ | (2.1)

Rm corresponde a la reluctancia del circuito magnético, ϕ indica la magnitud del

flujo, es decir, la cantidad de campo magnético que atraviesa una superficie y

Fmm es la fuerza magnetomotriz (que es distinta a la fuerza magnética Fm). La

ley de Hopkinson relaciona estos parámetros con la corriente que circula por el

bobinado (i) y la cantidad de vueltas de su núcleo (N).

Por otro lado, la inductancia del bobinado está dada por la ecuación 2.2

L ∗ i = N ∗ ϕ | (2.2)

El electroimán utilizado (figura 2.3) está compuesto por una pieza en forma de

E y otra en forma de I, que se encuentran separadas por un espacio o gap de

aire. Este circuito magnético se puede modelar como a un toroide con un corte o

separación de longitud lA = 2 ∗ yo, como se muestra en la figura 2.4

12

Figura 2.4: Toroide con gap de aire.

Partiendo del caso de un toroide sin gap de aire, se puede modelar su reluctancia

con la ecuación 2.3. En la que A es el área transversal, µr es la permeabilidad

relativa del material, µo es la permeabilidad magnética en el vacio y lh es la

longitud del circuito magnético.

Rm =

lh
µo ∗ µr ∗ A

(2.3)

Combinando las ecuaciones 2.1, 2.2, y 2.3, se llega a la expresión de la inductancia

del toroide sin gap de aire:

L =

N
i

∗ ϕ =

N
i

∗

N ∗ i
Rm

=

N² ∗ A ∗ µo ∗ µr
lh

(2.4)

Al agregar un gap de aire, se genera una discontinuidad en el medio magnético

de distancia lA (longitud en el aire).

El flujo magnético atraviesa esta discontinuidad sin desviaciones (siempre que lA

sea pequeña comparada con el área transversal A).

Al haber un gap de aire la reluctancia del sistema aumenta, por lo que se debe

Capítulo 2. Caracterización del Electroimán | 13

sumar, en serie a Rm, la reluctancia en el aire Ra. Por otro lado, lh prácticamente

no se ve modificada ya que es una pequeña incisión en el circuito magnético. De

esta forma, se obtiene la ecuación 2.5.

L =

N²
Rm ∗ Ra

=

N²

lh
A∗µo∗µr

+

la
A∗µo

=

N² ∗ A ∗ µo

la +

lh
µr

(2.5)

Debido a que la es el gap de aire, se debe reemplazar por la distancia de separación

entre las dos piezas magnéticas, que está representada por la variable yo. En el

caso de nuestro electroimán, las líneas de fuerza atraviesan dos veces y, por lo

tanto la = 2 ∗ yo.

Además, en la ecuación 2.5 µr ≫ 1 entonces 2∗yo ≫ lh
µr

, se obtiene la inductancia

en función de la distancia del gap de aire:

L(y) = N² ∗ A ∗ µo
2 ∗ yo

(2.6)

## 2.3. Cálculo de la fuerza magnética

La fuerza magnética de atracción que ejerce el electroimán sobre la pieza en

forma de I se puede modelar a partir de la energía almacenada en un inductor y

al considerar que esta es igual al trabajo:

E(i, y) = W =

Z
Fm ∗ dy => Fm =

∂E(i, y)
∂y | (2.7)

Siendo E(i, y) la energía que almacena un inductor en su campo magnético:

E(i, y) = L(i, y) ∗ i

2
2

(2.8)

La expresión anterior indica que la cantidad de energía que almacena el sistema

14

es función del gap de aire (y) y de la corriente que circula por el electroimán (i).

Combinando las ecuaciones 2.6, 2.7 y 2.8:

|Fm| =

∂E(i, y)
∂y =

i

2
2

∗

∂

N²∗A∗µo
2∗y
∂y =

i

2 ∗ N² ∗ µo ∗ A
4 ∗ y

2

(2.9)

Como se puede apreciar en la ecuación 2.9 la fuerza es proporcional al cuadrado

de la acción de control (es decir, de la corriente), e inversamente proporcional al

cuadrado de la variable que se desea controlar (es decir, de la distancia). Por lo

tanto, el problema adquiere un comportamiento no lineal.

## 2.4. Análisis del electroimán

Utilizando los datos de construcción del electroimán mencionados en el apartado

2.1 se puede determinar qué corriente será necesaria para sostener el objeto del

peso deseado.

Para obtener una expresión de diseño, partimos de la ecuación 2.9 y la igualamos

a la fuerza ejercida por el peso del objeto que se debe hacer levitar (|Fm| = m∗g):

m ∗ g =

i

2 ∗ N² ∗ µo ∗ A
4 ∗ y

2

(2.10)

De la ecuación 2.10, y a partir de las condiciones de diseño del problema, se puede

determinar la corriente necesaria para mantener el objeto en suspensión:

inom =

s
4 ∗ m ∗ g ∗ y

2
N² ∗ µo ∗ A

(2.11)

Considerando las condiciones mas exigentes para el sistema, con m = mmax =

30kg e y = ymax = 5mm:

Capítulo 2. Caracterización del Electroimán | 15
inom = 20,4A | (2.12)

Aunque esta corriente es suficiente para mantener el objeto en estado de equilibrio,

se necesita una corriente mayor para poder responder ante perturbaciones en la

distancia de separación, por lo tanto se define la corriente máxima imax = 30A.

## 2.5. Expresión de inductancia linealizada

Volviendo a la ecuación 2.6, se realiza una expansión por serie de Taylor y se

desprecian los términos de orden mayor o igual a 2, con el objetivo de llegar a

una expresión lineal para la inductancia se obtiene:

L(y)[mH] = −2,2089 ∗ y[mm] + 17,67[mH] | (2.13)

## 2.6. Mediciones sobre el electroimán

esto iría acá??

## 2.7. Modelo de estado de la planta

Al plantear un diagrama de cuerpo aislado del sistema | poner imagen | y plantear

la sumatoria de fuerzas en el eje y:

XFy = m ∗ a => m ∗ g − Fm = m ∗ y¨ | (2.14)

De la ecuación 2.9 se convierte la ecuación 2.14 en:

16

m ∗ y¨ = m ∗ g − K ∗

i(t)

2
y(t)

2

(2.15)

Donde K es una constante de valor:

K =

N² ∗ µo ∗ A
4

= 1,77 ∗ 10⁻⁵
[

N ∗ m²
A²
] | (2.16)

Teniendo en cuenta que i(t) es la entrada a la planta, se puede plantear un modelo

con las siguientes variables de estado:

se puede poner mas grande??

x1 = y(t) | (2.17)
x2 = ẋ1 | (2.18)
u = i(t) | (2.19)

Por lo tanto se obtienen dos ecuaciones de estado:

x˙1 = x2 | (2.20)

x˙2 = g −

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
| (2.21)

El modelo es no lineal, por lo tanto se utiliza el método de linealización por

serie de Taylor. En primer lugar se deben encontrar los puntos de equilibrio del

sistema; por las condiciones del problema se define x1o = 4mm. El resto de los

puntos de equilibrio se encuentra igualando las derivadas a cero:

x1o = 4mm | (2.22)
x2o = 0 | (2.23)

Capítulo 2. Caracterización del Electroimán | 17

uo =

r
m ∗ g
K
∗ x1o | (2.24)

Por lo tanto las ecuaciones linealizadas quedan:

x˙1 = x2 | (2.25)

x˙2 = 2 ∗

K ∗ u

2
o
m ∗ x

3
1o

∗ x1 − 2 ∗

K ∗ uo
m ∗ x

2
1o
∗ u | (2.26)

Las matrices del modelo quedan:

A =

0 1

2∗g
yo

0

- (2.27)

B =

0

−

2
yo

∗

qK∗g

m

- (2.28)

C =

1 0
(2.29)

Es posible obtener la función transferencia de la planta utilizando:

Gplanta = C ∗ (S ∗ I − A)

−1
∗ B | (2.30)

Finalmente, se obtiene para m = 30kg e yo = 4mm:

Gplanta = −

2
yo

∗

qK∗g

m
S² −

2∗g
yo

=

−1,201
S² − 4900

(2.31)

La planta tiene dos autovalores en + −

q2∗g
yo

= + − 70[ rad
s

]. Es decir, uno en

el semiplano izquierdo y otro en el derecho, lo que provoca que la planta sea

inestable y se deba buscar una estrategia de control apropiada para controlarla.

18

Al trabajar con una planta cuya masa es variable, conviene dejar m como incógni-

ta:

Gplanta(m) = −

r
30
m

∗

1,201
S² − 4900

(2.32)

De la transferencia de la planta en 2.32 se observa que la ganancia del sistema

depende de la masa del objeto, pero no se modifica la ubicación de los polos. A

menor masa, mayor es la ganancia del sistema; Se debe escoger una estrategia de

control que tenga en cuenta los cambios que puede sufrir la ganancia del sistema.

# Capítulo 3

# Controlador de corriente

## 3.1. Diseño y modelado

Para regular la fuerza ejercida por el electroimán es necesario controlar la corriente

que circula por él. Para ello, se modela a la planta como la impedancia de un

inductor con una resistencia serie, cuya inductancia varía con el gap de aire:

1
sL(y) + RL

(3.1)

Para realizar este control se utiliza un sistema realimentado, como el que se

muestra en la figura 3.1. Se puede ver que se ingresa con una tensión de referencia

(Vin) proporcional a la corriente de salida deseada, que luego se multiplica por la

ganancia de entrada (Kin). La corriente del electroimán se realimenta en forma de

una tensión proporcional a ella (ViF ). Ambas tensiones son restadas y el resultado

(e) ingresa al bloque de comparador con histéresis, que actúa en conmutación,

por lo que su salida tiene dos estados posibles: ±VL.

Al ser aplicadas al inductor se producirá una rampa de corriente: si la tensión

es positiva, la rampa crece, y si es negativa decrece. De esta forma, debido a la

19

20

conmutación del comparador se obtiene, a la salida, una forma de onda triangular

IL, cuyo valor medio es la corriente deseada y se corresponde a la tensión de

referencia.


Figura 3.1: Diagrama en bloques simplificado del controlador de corriente.

### 3.1.1. Características del sistema

Para sensar la corriente se utiliza un sensor de efecto Hall HO 15-NP, con

una transconductancia de H(s) = 53.3 mV/A.

Para la ganancia de entrada Kin se utiliza un valor de 0.32 puesto que Vin

varía entre 0 V y 5 V y debe mapearse con una corriente variable entre 0

A y 30 A.

Se adopta una variación de la corriente en torno a su valor medio (ripple)

de 500 mA, por lo que resulta en un ancho de histéresis de 26.665 mV.

Según mediciones realizadas sobre el electroimán, la inductancia en el punto

de equilibrio y0=4mm es de 16.44 mHy (considerando la inductancia de

dispersión de 8.89 mHy) y la resistencia serie es de 0.2 Ω.

La tensión aplicada sobre el electroimán es +24 V para el estado ON y -24

V para el estado OFF.

Capítulo 3. Controlador de corriente | 21

Se utiliza un driver de corriente que trabaja en conmutación mediante un

puente H con 4 N-MOS.

### 3.1.2. Circuito del controlador de corriente

Se plantea la etapa de entrada que consiste en la ganancia Kin y el restador con

la realimentación. El objetivo es imponer una ganancia de entrada de 0.32, y que

la salida de esta etapa tenga un punto de operación de 2.5V para poder utilizar

una fuente de alimentación entre 0 y 5 V para los operacionales. Para lograr esto

se utiliza un circuito como el que se muestra en la figura 3.2.

Figura 3.2: Etapa de entrada.

Para la implementación del comparador con histéresis se utiliza un amplificador

22

operacional realimentado positivamente. Se implementa un ancho de histéresis de

26.665 mV, alrededor de un punto de operación de 2.5 V, como se muestra en la

figura 3.3.

Figura 3.3: Comparador con histéresis.

Para controlar la corriente en el electroimán se utiliza una topología en puente H,

que permite conmutar la polaridad de la tensión aplicada a la bobina. Para medir

la corriente se utiliza un sensor de efecto Hall, que es modelado en la simulación

como una fuente de tensión controlada por corriente, con una ganancia de 53.3

mV/A correspondiente a su transconductancia. Esta implementación puede ob-

servarse en la figura 3.4. A continuación, su salida es realimentada a la etapa de

entrada luego de restarle la tensión de referencia Vbias de 2.5V, como se muestra

en la figura 3.5.

Capítulo 3. Controlador de corriente | 23


Figura 3.4: Puente H y sensor de efecto Hall.

Figura 3.5: Resta del Vbias al sensor de efecto Hall.

### 3.1.2.1. Simulaciones de formas de onda

En la figura 3.6 se pueden observar dos formas de onda. La inferior se corresponde

con la salida del comparador con histéresis y la superior con la corriente en el

24

electroimán. Para la simulación se utilizó una tensión de referencia de entrada de

1 V, por lo tanto el valor medio de la corriente en la salida es 6 A con un ripple

de 500 mA.


Figura 3.6: Formas de onda de corriente en el electroimán y salida del comparador.

### 3.1.2.2. Simulación de un escalón en la referencia de corriente

En la figura 3.7 se muestra cómo cambia la corriente en el electroimán al aplicarle a

la entrada del controlador un escalón de tensión entre 1 V y 3 V. Se puede observar

cómo la conmutación del comparador se detiene para ajustar la corriente con la

referencia.

Capítulo 3. Controlador de corriente | 25

Figura 3.7: Respuesta al escalón del circuito.

### 3.1.2.3. Descripción general de la topología

La corriente que se desea controlar es la que circula por el electroimán y, debido a

que el sistema va a trabajar con corrientes elevadas, es importante que la imple-

mentación del controlador de corriente sea eficiente. Por lo tanto, para disminuir

la disipación de potencia del circuito se utiliza un controlador que funciona en

conmutación.

Para lograr una corriente contínua en el electroimán utilizando una fuente con-

mutada se debe alternar la polaridad de la tensión aplicada en los bornes del

inductor. Al hacer esto, la corriente crece y decrece (según la polaridad) con

forma exponencial debido a la resistencia interna del electroimán. Sin embargo,

como el intervalo de tiempo de esta conmutación es pequeño comparado con la

constante de tiempo de la planta, el incremento de corriente será pequeño y puede

ser aproximado a una recta. Por lo tanto se obtiene una corriente contínua con

un ripple superpuesto de forma triangular.

Para lograr alternar la polaridad de la fuente sobre el inductor se utiliza una

topología en puente H con 4 MOSFET que funcionan con un ciclo de trabajo

26

determinado (manejado por el controlador por histéresis) como se observa en la

figura 3.8. Pueden diferenciarse dos semiciclos de trabajo: uno de estado ON y

otro de estado OFF. El primero se define como el semiciclo durante el cual la

corriente en el inductor crece (pendiente positiva), mientras que el segundo se da

cuando la corriente decrece.

Figura 3.8: Topología elemental del puente H.

El electroimán se conecta entre los puntos medios de cada par de transistores.

De esta manera se puede conmutar la polaridad de la tensión que se le aplica.

Sólo se permite que dos transistores se enciendan a la vez, y esto se realiza de

manera diagonal. Es decir, en la figura 3.8, Q1 y Q4 pueden estar encendidos,

mientras que Q3 y Q2 están apagados, y viceversa. De otra forma, se podría

generar un cortocircuito entre la fuente de alimentación y GND, que produciría

una circulación de corriente denominada shoot-through.

Los 4 MOSFET utilizados para el puente H son de tipo N. Para que estos puedan

funcionar correctamente en conmutación es necesario que en el estado ON, la

Capítulo 3. Controlador de corriente | 27

diferencia de tensión entre gate y source sea mayor o igual a 7 V. Esto no es un

problema para los dos MOS inferiores del puente H (Q2 y Q4), ya que la tensión

en source está fijada en GND y el driver puede aplicar 12 V al gate (superando

los 7 V entre gate y source). El problema radica en los transistores superiores

del puente H, ya que la tensión en source varía entre 0 V y 24 V, por lo que en

el gate debería haber, por lo menos, 31 V con respecto a GND. Sin embargo, la

tensión máxima disponible entregada por la fuente es de 24 V. Para resolver este

problema se utiliza un driver flotante con bootstrap.

Para controlar la conmutación se utiliza un mosfet driver HIP4081A que se en-

carga de encender y apagar los transistores según las entradas de control. Además

permite la configuración de un tiempo muerto para evitar que se enciendan dos

transistores de un lado a la vez. También provee la circuitería necesaria para

implementar la fuente flotante que enciende los mosfet del lado superior para lo

cual solo se debe agregar un diodo y un capacitor de manera externa. Para la

implementación circuital se van a utilizar los MOSFET IPB160N04.

En la figura 3.9 se observa solo una de las mitades del puente H (lado A) junto

con las señales de control provistas por el driver HIP4081A. El análisis para la

otra mitad es análogo, por lo que se evita por simplicidad. La implementación

del driver bootstrap permite obtener en el gate del MOS superior, una tensión de

36 V respecto a GND, logrando así una diferencia de tensión mayor a 7 V entre

gate y source.

28


Figura 3.9: Configuración Bootstrap simplificada.

El driver bootstrap consiste en un capacitor (CBS), un diodo, y la circuitería

interna del HIP4081A. Para garantizar el correcto funcionamiento del bootstrap,

al encender el sistema, la secuencia de inicio del HIP4081A enciende las dos

salidas de la parte inferior del puente H: ALO y BLO con el fin de encender Q2

y Q4 durante un tiempo que se conoce como periodo de refresco de bootstrap.

De esta forma, los capacitores de bootstrap de ambos lados quedan conectados a

GND y se pueden cargar completamente. Durante este tiempo, las salidas a los

gates AHO y BHO se mantienen en bajo continuamente lo que asegura que no se

produzca corriente de shoot-through durante el período nominal de refresco del

bootstrap. Al final de este período las salidas responden normalmente al estado

de las señales de entrada de control.

Para comprender su funcionamiento se hará un breve análisis del sistema. Para

ello, se parte suponiendo que el sistema se encuentra funcionando: con el transistor

Capítulo 3. Controlador de corriente | 29

Q2 encendido (ALO = VCC), Q1 apagado (AHO = AHS = 0 V) y la corriente

circulando de izquierda a derecha como lo indica la figura 3.9. En ese caso, el

capacitor CBS se carga a 12 V, ya que en un terminal tiene la fuente de 12 V (a

través del diodo DBS) y el otro está conectado a GND por medio de Q2.

Una vez que se apaga el transistor inferior, empieza a transcurrir el tiempo muerto.

Teniendo en cuenta que la carga es inductiva, el valor medio de la corriente

mantiene su sentido circulando por los diodos antiparalelos del MOS inferior del

lado A y el superior del lado B. Esto provoca que el source del MOS superior del

lado A tenga una tensión negativa igual a la caída de tensión en directa del diodo

antiparalelo de Q2.

Una vez finalizado el tiempo muerto, se enciende el MOS Q1. Para encenderlo,

la señal AHO se pone en nivel alto. Durante el tiempo que Q1 pasa de estar

apagado a encendido, la tensión en el source cambia de −Vd a Vbus de manera

gradual mientras se carga el gate, y AHO pasa a ser igual a AHB, que es igual

a la tensión entregada por el capacitor de bootstrap sumada a la tensión en el

source de Q1. De esta manera se logra una tensión de 36 V con respecto a GND

en el gate y genera una diferencia entre gate y source de 12 V.

Para lograr un funcionamiento adecuado del Boostrap es necesario dimensionar

correctamente al capacitor CBS con el fin de que pueda proveer la carga suficiente

durante el tiempo en el que el MOS esté encendido.

### 3.1.2.4. Dimensionamiento de capacitor de bootstrap

Para el dimensionamiento se tuvieron en cuenta sugerencias y procedimientos

descriptos en [1] y [2].

Para encender un NMOS es necesario proveer corriente a su gate hasta cargar las

capacidades parásitas entre gate-source y gate-drain. Una vez cargadas, el MOS

queda en estado encendido y no consume más corriente en el gate. En el caso de

30

los MOS del lado superior, esta corriente proviene del capacitor de bootstrap.

En la implementación del puente H se decidió colocar resistencias entre gate y

source. Estas aparecen como R1, R2, R3 y R4 en la figura 3.10. Debido a la

diferencia de tensión entre gate-source, se genera una corriente constante en estas

resistencias durante el tiempo que el MOS esté encendido, que también debe ser

provista por el bootstrap.

Figura 3.10: Puente H.

Por otro lado, el capacitor debe entregar corriente al diodo de bootstrap cuan-

do este queda en inversa (IDR ), y también entregar una corriente de fuga al

circuito integrado HIP (IQBS ). Esta última se desprecia ya que es compensada

internamente por la bomba de carga del HIP.

Por lo tanto, para poder dimensionar correctamente el capacitor de bootstrap es

necesario tener en cuenta todos estos efectos mencionados anteriormente. Para

Capítulo 3. Controlador de corriente | 31

ello se parte planteando la carga que almacena el capacitor bootstrap:

QB = CB ∗ VB | (3.2)

En la ecuación 3.2, QB es la carga total del capacitor de bootstrap, CB es la propia

capacidad del capacitor, y VB es la diferencia de tensión entre sus terminales.

Para evitar sufrir una caída de tensión tal que afecte el encendido de los MOS,

es necesario que QB pueda abastecer también al gate, a la resistencia entre gate-

source y al diodo en inversa. Por lo tanto:

QB > QG + QRR +

IDR + IGS

fPWM

(3.3)

Donde:

QG= Carga total que se debe entregar al gate del MOS.

QRR = Carga entregada al diodo en inversa durante el tiempo de recovery

(cuando pasa de modo conducción a inversa).

IDR = Corriente de fuga del diodo en inversa

IGS = Corriente que circula por la resistencia de gate-source

fPWM = frecuencia de conmutación

Por lo tanto, al reemplazar la ecuación 3.2 en la 3.3 se obtiene:

CBS >

QG + QRR +

IDR+IGS
fPWM
∆VB

(3.4)

Según la hoja de datos [5] del MOSFET IPB160N04, QG= 170 nC. Por lo tan-

to, adoptando una caída de tensión tolerable en el capacitor de ∆VB = 0.1 V y

32

considerando la información brindada por las hojas de datos, es posible dimensio-

nar el capacitor para que este posea una carga suficiente para mantener siempre

encendido al MOSFET utilizando la inecuación 3.4 .

Para el cálculo de la carga de recuperación QRR se puede considerar que la forma

de onda de la corriente de recuperación es triangular. De esta forma, QRR es

aproximadamente igual a la mitad del producto entre el pico de la magnitud de

corriente inversa y la duración del tiempo de recuperación. Debido a que se usa

el diodo RSX205LAM30TR, se obtiene a partir de [3] que IR es igual a 0.1 A y

el tiempo de recuperación de inversión es de 12.5 ns. Por lo tanto, la carga de

recuperación resulta de 0.625 nC.

Para la corriente inversa de fuga del diodo de bootstrap se obtiene un valor de

IDR=2 mA (@ T=75°, VR= 24V).

La corriente IGS tiene forma exponencial pero se aproxima a una constante debido

a que el intervalo de tiempo es pequeño. Por lo tanto, puede calcularse como la

diferencia de tensión del capacitor de bootstrap (VB=12V) dividido el valor de la

resistencia gate-source. Esta resistencia es de 4.7 kOhm. Por lo tanto IGS=2.55

mA.

Debido a que el controlador por histéresis no asegura que haya una conmutación

en un tiempo constante (como se observa en la figura 3.7), se decidió superponer

una conmutación auxiliar de 50 kHz.

CBS >

QG + QRR +

IDR+IGS
fPWM
∆VB

>

170nC + 0,625nC +

2mA+2,55mA
50KHz
0,1V
F | (3.5)
CBS > 2,61µF | (3.6)

Capítulo 3. Controlador de corriente | 33

Por lo tanto, una capacidad mayor a 2,61µF resultará en una caída menor a 0.1

V en el capacitor de bootstrap durante el tiempo de encendido de los MOSFET.

Podría usarse un capacitor más pequeño, a costa de permitir una mayor caída de

tensión en el capacitor.

Finalmente, se decidió utilizar 2 capacitores de bootstrap en paralelo de 5,6µF

cada uno con el objetivo de reducir la resistencia serie.

### 3.1.2.4.1 Resistencia entre gate y source

Se colocan resistencias que conectan el gate y el source de cada MOS en el puente

H. Estas se observan en la figura 3.10 como R1, R2, R3, R4. Su propósito es

evitar que el gate del mosfet se encuentre cargado cuando el circuito se enciende

y el driver de corriente aún no puede descargarlo. Además ayuda a evitar que se

encienda el mosfet por ruido acoplado capacitivamente.

Se utiliza una resistencia de 4.7 kΩ debido a que permite que el gate se descargue

en un tiempo rápido, consumiendo solo 2.55 mA del capacitor de bootstrap.

### 3.1.2.4.2 Protección del gate

El gate de los MOS es sensible a las sobretensiones. Soporta como máximo ±20V.

Una descarga electrostática (ESD) puede sobrepasar ampliamente este valor de

tensión, pudiendo dañar el MOS al acercar la mano o la sonda del osciloscopio.

Para protegerlo en estos casos se coloca un diodo TVS entre el gate y source, de

manera de limitar la tensión que se desarrolla en el gate a un valor seguro.

Se eligen los TVS SMAJ15 con una tensión bidireccional de ±15V. y se colocan

entre el gate y source de cada transistor.

34

### 3.1.2.4.3 Tiempo muerto

Para evitar generar un cortocircuito durante la conmutación de los transistores,

el driver HIP4081A permite configurar un tiempo muerto que debe transcurrir

desde que se apaga un transistor y se enciende el próximo. Esto se configura

mediante dos resistencias conectadas a los pines LDEL y HDEL del HIP4081A.

Para saber el tiempo muerto necesario, debe conocerse el tiempo que tarda en

apagarse un mosfet IPB160N04. De [5] se obtiene que este tiempo es 63 ns. Este

valor se obtiene de tener en cuenta el TOF F y el TF ALL de la hoja de datos . Por

lo tanto se elige que el deadtime sea de 100 ns, para tener un margen, además de

que esta aplicación específica no requiere un tiempo de encendido rápido de los

mosfets.

Según la hoja de datos del HIP4081A, para obtener ese tiempo muerto, las resis-

tencias en HDEL y LDEL deben ser 200 KΩ.

### 3.1.2.5. Dimensionamiento de los capacitores de fuente

Para reducir el consumo de potencia de la red se utilizan capacitores en paralelo

a la fuente de +24V. Esto permite que, una vez que la fuente cargó inicialmente

el inductor, en las conmutaciones sucesivas la carga del inductor pase a dichos

capacitores en un semiciclo y viceversa en el otro ciclo de conmutación. Idealmen-

te, esta transferencia de energía no tiene pérdidas. Por lo tanto, el consumo de

potencia queda reducido a la perdida por disipación de los MOSFET y los demás

componentes del controlador de corriente.

Estos capacitores deben tener una baja resistencia equivalente serie (ESR) ya

que, de lo contrario, disipan mucha potencia en forma de calor y se acorta su

vida útil. Además generan ripple en la tensión VBUS.

En la figura 3.10 los capacitores de la fuente están representados por C1 y C2.

Capítulo 3. Controlador de corriente | 35

Para poder dimensionarlos correctamente hay que tener en cuenta que la forma

de onda de la corriente que circula por el electroimán en régimen permanente

es aproximadamente triangular. Esta corriente es conducida durante medio ciclo

desde estos capacitores y hacia el electroimán por Q1 y Q4. Luego, durante la otra

mitad del ciclo, la corriente regresa a estos capacitores a través de Q2 y Q3. Esto

provoca que la corriente en los capacitores sea, durante el semiciclo encendido,

igual al valor medio de la corriente del electroimán, con ±

∆IL
2

. Similarmente

ocurrirá en el semiciclo apagado, pero con valor medio −IL. Por lo tanto, la

corriente tendrá la forma que se muestra en la figura 3.11

Figura 3.11: Forma de onda de la corriente en C1 y C2.

Sabiendo que por el electroimán circulará una corriente media de 21 A en condi-

ciones normales de trabajo, la carga del capacitor se puede calcular como:

36

∆Q =

Z
Idt

∆Q

+ =

TS
2

∗ ∆IL ∗

1
2

+ (< IL > −

∆IL
2

) ∗

TS
2

∆Q

+ =< IL > ∗

TS
2

(3.7)

Considerando ∆IL = 500mA y T = 0,47ms que corresponde a Y = 2mm según

la tabla 3.1

∆Q = 21A ∗

0,47ms
2
≈ 5mC | (3.8)

Al considerar que un ripple de V=500 mV es aceptable, se obtiene un valor de:

c =

∆Q
∆V
= 10mF | (3.9)

Para obtener este valor de capacidad utilizamos varios capacitores en paralelo

para disminuir la ESR, como se muestra en la figura 3.12. Esto es porque por los

capacitores circula una corriente de hasta 21.25 A. Por lo tanto, al colocarlos en

paralelo se reduce la corriente que circula (en partes iguales), por cada capacitor:


Figura 3.12: Capacitores de la fuente.

Capítulo 3. Controlador de corriente | 37
C = C1 + C2 + ... + Cn | (3.10)

Si todos los valores de ESR son iguales obtenemos

RT =

RESR
n

(3.11)

Por lo tanto reemplazando se puede calcular la potencia que disipan como:

P = I

2

∗ RT = 21,25²
∗

RESR
n

(3.12)

Se decidió utilizar 6 capacitores de 2200 uF/50V con una ESR de 17 Ω (datos obtenidos de [4]) .

Por lo tanto reemplazando en la ecuación 4.4 se obtiene que la potencia disipada

es de:

P = 1,28W | (3.13)
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

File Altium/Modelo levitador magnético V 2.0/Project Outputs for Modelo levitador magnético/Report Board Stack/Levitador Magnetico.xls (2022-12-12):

Board Stack Report
Stack Up |  | Layer Stack
Layer | Board Layer Stack | Name | Material | Thickness | Constant
1 |  | Top Paste
2 |  | Top Overlay
3 |  | Top Solder | Solder Resist | 0,010mm | 3,5
4 |  | Top Layer | Copper | 0,036mm
5 |  | Dielectric 1 | FR-4 | 1,500mm | 4,2
6 |  | Bottom Layer | Copper | 0,036mm
7 |  | Bottom Solder | Solder Resist | 0,010mm | 3,5
8 |  | Bottom Overlay
9 |  | Bottom Paste
 | Height : 1,591mm

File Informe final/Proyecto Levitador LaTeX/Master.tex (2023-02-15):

% !TeX spellcheck = es_ES
\documentclass[twoside,openright,spanish,12pt,Grado]{licthesis_modIV}%,mydraft

% librerias de circuitos
%\usepackage{pstricks,pstricks-pdf,pst-node,pst-circ,pst-plot,pst-3dplot,pst-all}
\usepackage[siunitx]{circuitikz}
\usepackage[utf8]{inputenc}
\usepackage[siunitx]{circuitikz}
\usepackage[utf8]{inputenc}
\pagestyle{empty}
\usepackage{tikz}
\usetikzlibrary{shapes,arrows,positioning,babel}
\usetikzlibrary{decorations.markings}
\usepackage{xcolor}
\usepackage{listings}

\definecolor{mGreen}{rgb}{0.1,0.6,0}
\definecolor{mGray}{rgb}{0.5,0.5,0.5}
\definecolor{mPurple}{rgb}{0.80,0,0.82}
\definecolor{backgroundColour}{rgb}{0.95,0.95,0.92}
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
\def\subxb#1.#2\relax{#2}

\newcommand{\se}[1]{{
    \mathrm{\uppercase{\substring{#1}{1}{1}}}
    _\mathrm{\uppercase{\substring{#1}{2}{2}}}
    \mathrm{\uppercase{\substring{#1}{3}{3}}}
    _\mathrm{\uppercase{\substring{#1}{4}{4}}}
    \mathrm{\uppercase{\substring{#1}{5}{5}}}
    _\mathrm{\uppercase{\substring{#1}{6}{6}}}}}

%********************Separado en silabas correcto******************************************************
\hyphenation{na-tu-ral trans-fe-ren-cia res-pues-tas consta mo-du-la-cion cons-tru-ir co-rrien-te}
\hyphenation{su-mi-nis-trar e-fec-tua-das ins-pi-ra-do sa-cri-fi-cio erro-res esta-ble-ci-mien-to}
\hyphenation{aproxi-ma-das pre-sin-cro-nis-mo megadiscap}
%********************Separado entre párrafos******************************************************
\usepackage{parskip}
\setlength{\parindent}{0pt}
%*************************Comienzo del documento Tesis*************************************************

\makeindex
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

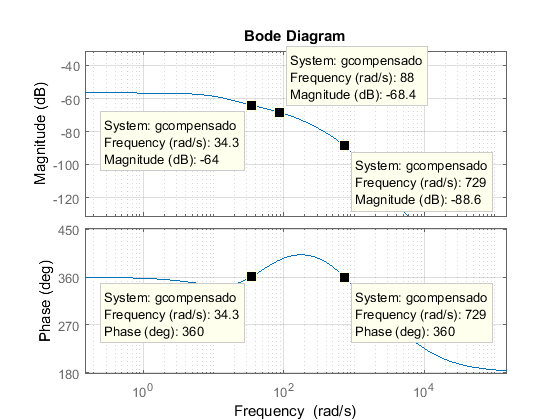
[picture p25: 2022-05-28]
Informe final/Proyecto Levitador LaTeX/Informe/7-ImplementacionDigital/figuras/Bode-compensado-para-k-1.png

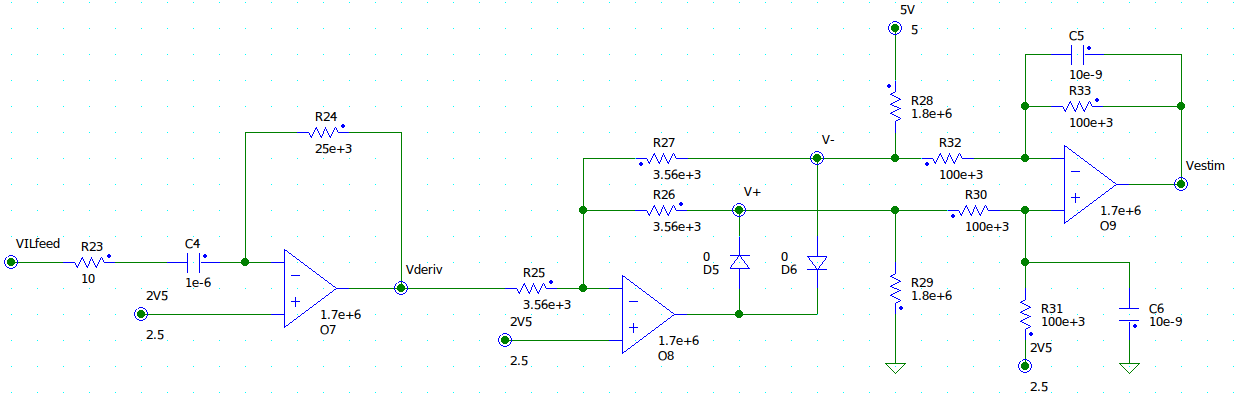
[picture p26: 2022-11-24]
Informe final/Proyecto Levitador LaTeX/Informe/5-EstimadorAnalogico/figuras/simulacion_derivador+rectificador.png

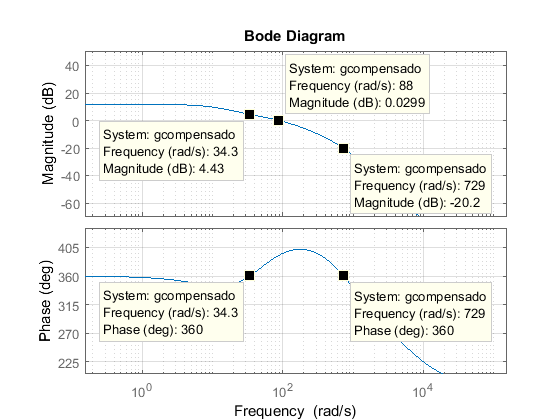
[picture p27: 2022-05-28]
Informe final/Proyecto Levitador LaTeX/Informe/7-ImplementacionDigital/figuras/Bode-compensado-para-k-2630.png

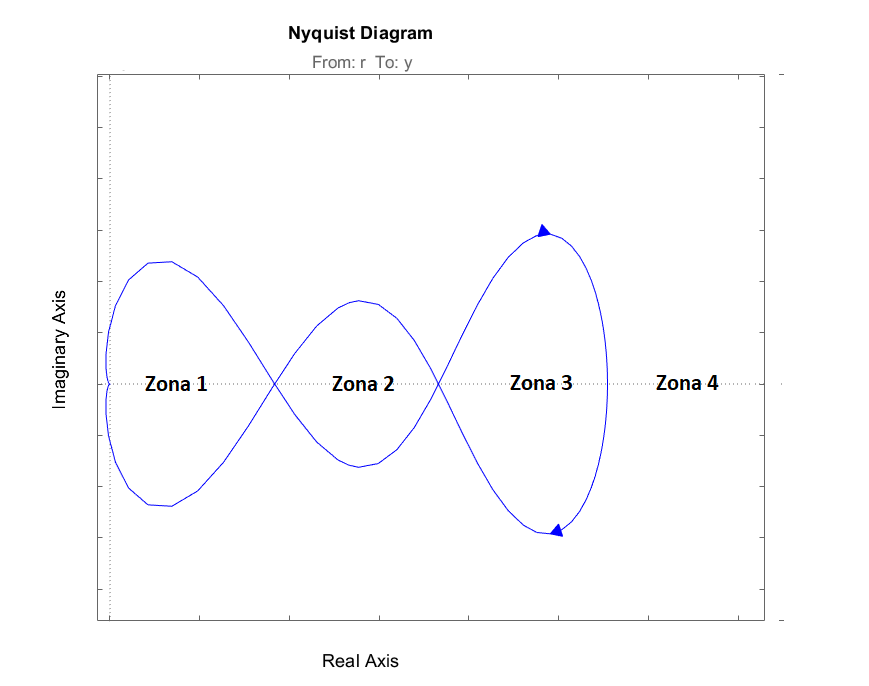
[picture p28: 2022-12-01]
Informe final/Proyecto Levitador LaTeX/Informe/7-ImplementacionDigital/figuras/Nyquist-deseado-dig.png

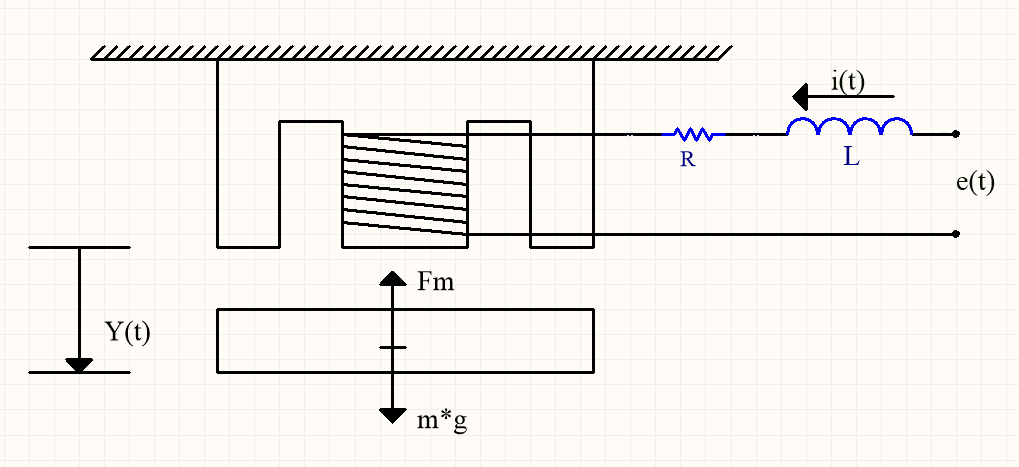
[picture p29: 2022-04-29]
Informe final/Proyecto Levitador LaTeX/Informe/3-CaracterizacionElectroiman/figuras/modelo-fisico.png

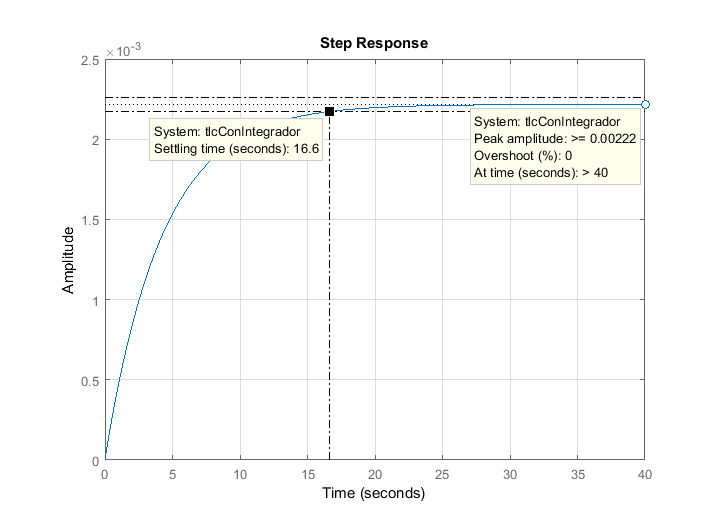
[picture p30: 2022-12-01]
Informe final/Proyecto Levitador LaTeX/Informe/6-CompensadorAnalogico/figuras/stepresponseintegradorkint_1_m_30.png

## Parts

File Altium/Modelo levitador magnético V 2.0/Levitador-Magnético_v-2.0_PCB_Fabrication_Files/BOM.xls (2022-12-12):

Designator | Value | Comment | Description | Quantity | Mfr PN | Manufacturer
C100, C102, C104, C110, C111, C112, C125, C126, C127, C128, C129, C206, C207, C208, C301, C302, C405, C410, C505, C506 | 0.1uF | Capacitor | CAP CER 0.1UF 50V X7R 1206 | 20 | C1206X7R500-104KNE | Venkel
C101, C200, C303, C304, C502 | 1uF | Capacitor | CAP CER 1UF 25V X7R 1206 | 5 | GMC31X7R105M25NT | CAL-CHIP ELECTRONICS, INC.
C103 | 900pF | Capacitor | CAP CER 910PF 50V NP0 1206 | 1 | C1206C911J5GAC7800 | KEMET
C105, C106, C123, C124 | 5.6uF | Capacitor | CAP CER 4.7UF 50V X7R 1206 | 4 | CL31B475KBHNFNE | Samsung Electro-Mechanics
C107, C108, C109 | 2uF | Capacitor | CAP1206 X5R 2.2UF 20% 35V | 3 | GMC31X5R225M35NT | CAL-CHIP ELECTRONICS, INC.
C113, C114, C115, C116, C117, C118 | 2200uF | EKY-350ELL102MK25S | CAP ALUM 2200UF 20% 35V RADIAL | 6 | EKY-350ELL222MM25S | United Chemi-Con
C119 | 4.7nF | Capacitor | CAP CER 4700PF 200V X7R 1206 | 1 | GMC31X7R472K200NT | CAL-CHIP ELECTRONICS, INC.
C120, C122 | 47nF | Capacitor | CAP CER 0.047UF 50V C0G/NP0 1206 | 2 | GMC31CG473J50NT | CAL-CHIP ELECTRONICS, INC.
C121 | 10uF | Capacitor | CAP CER 10UF 16V X7R 1206 | 1 | GMC31X7R106M16NT | CAL-CHIP ELECTRONICS, INC.
C201, C202, C203, C300 | 22uF | Capacitor | CAP CER 22UF 16V X5R 1206 | 4 | CL31A226MOCLNNC | Samsung Electro-Mechanics
C204 | 220nF | Capacitor | CAP CER 0.22UF 50V X7R 1206 | 1 | CL31B224KBFNNNE | Samsung Electro-Mechanics
C205 | 47uF | Capacitor | CAP CER 47UF 10V X5R 1206 | 1 | LMK316BJ476ML-T | Taiyo Yuden
C400, C403 | 18nF | Capacitor | CAP CER 0.018UF 100V X7R 1206 | 2 | C1206C183K1RAC7800 | KEMET
C401 | 150nF | Capacitor | CAP CER 0.15UF 50V X7R 1206 | 1 | 12065C154KAT2A | KYOCERA AVX
C402, C407 | 270pF | Capacitor | CAP CER 270PF 50V C0G/NP0 1206 | 2 | C1206C271J5GAC7800 | KEMET
C404, C406 | 1.6uF | Capacitor | CAP CER 1.5UF 10V X7R 1206 | 2 | CC1206KKX7R6BB155 | YAGEO
C408, C409 | 16nF | Capacitor | CAP CER 0.016UF 50V C0G/NP0 1206 | 2 | GRM3195C1H163JA01D | Murata Electronics
C500, C504 | 10nF | Capacitor | CAP CER 10000PF 500V X7R 1206 | 2 | C1206C103KCRAC7800 | KEMET
C501 | 1nF | Capacitor | CAP CER 1000PF 2KV X7R 1206 | 1 | 202R18W102KV4E | Johanson Dielectrics Inc.
C503 | 470pF | Capacitor | CAP CER 470PF 1KV C0G/NP0 1206 | 1 | CL31C471JIHNNNE | Samsung Electro-Mechanics
C507 | 5.14uF | Capacitor | CAP CER 5100PF 100V NP0 5% 1206 | 1 | C1206C512J1GAC7800 | KEMET
D100, D101, D104, D106, D108, D109, D110, D111, D200, D201, D202, D500, D501 |  | RSX205LAM30TR | DIODE SCHOTTKY 30V 2A PMDTM | 13 | RSX205LAM30TR | [NoParam], ROHM Semiconductor
D102, D103, D105, D107 |  | SMAJ15A | TVS DIODE 18VWM 29.2VC DO214AC | 4 | SMAJ18A | Littelfuse Inc.
D203, D204, D205, D403 |  | LED | 1206 RED SMD LED | 4 | L152L-LIC | American Opto Plus LED
D400, D401, D402 | 3V6 | Diodo Zener | DIODE ZENER 3.6V 3W SMB | 3 | 1SMB5914BT3G | onsemi
F200 |  | Fuse | FUSE 500MA 125VAC FAST 1206 | 1 | C1F 500 | Bel Fuse Inc.
J100, J200, P100, P101, P500, P501 |  | Header 2 | TERM BLK 2P SIDE ENT 2.54MM PCB | 6 | 282834-2 | TE Connectivity AMP Connectors
J400 |  | DB9H | CONN D-SUB RCPT 9POS R/A SLDR | 1 | A-DF 09 A/KG-T4S | Assmann WSW Components
P1, P2, P102, P300 |  | Header 3 | TERM BLK 3P SIDE ENT 2.54MM PCB | 4 | 282834-3 | TE Connectivity AMP Connectors
Q100, Q101, Q102, Q103 |  | IPB160N04 | MOSFET N-CH 40V 160A TO263-7 | 4 | IPB160N04S3H2ATMA1 | Infineon Technologies
R1 | 316 | 316 | RES 316 OHM 1% 1/4W 1206 | 1 | RMCF1206FT316R | Stackpole Electronics Inc
R2 | 1k | Potenciometro | POT 1K OHM 0.08W CARBON LINEAR | 1 | PDB12-H4251-102BF | Bourns Inc.
R3 | 4k99 | 4k99 | RES 4.99K OHM 1% 1/4W 1206 | 1 | RMCF1206FT4K99 | Stackpole Electronics Inc
R100 | 3k2 | 3k2 | RES 3.2K OHM 1% 1/4W 1206 | 1 | RN73H2BTTD3201F25 | KOA Speer Electronics, Inc.
R101, R102, R107, R108, R112, R124, R319, R323, R400, R401, R406, R410 | 10k | 10k | RES 10K OHM 1% 1/4W 1206 | 12 | RC1206FR-0710KL | YAGEO
R103, R113, R114, R115, R116, R122, R204, R301, R302, R303, R304, R306, R308, R310, R321, R322, R405, R409, R513, R515 | 1k | 1k | RES 1K OHM 1% 1/4W 1206 | 20 | RMCF1206FT1K00 | Stackpole Electronics Inc
R104, R109 | 500 | 500 | RES SMD 500 OHM 0.1% 0.3W 1206 | 2 | Y1625500R000B9W | Vishay Foil Resistors (Division of Vishay Precision Group)
R105, R117, R118, R125, R126, R202 | 4k7 | 4k7 | RES 4.7K OHM 1% 1/4W 1206 | 6 | RMCF1206FT4K70 | Stackpole Electronics Inc
R106, R509 | 15k | 15k | RES 15K OHM 1% 1/4W 1206 | 2 | CRCW120615K0FKEAC | Vishay Dale
R110, R119, R120, R312, R313, R318, R320 | 200k | 200k | RES 200K OHM 1% 1/4W 1206 | 7 | RC1206FR-07200KL | YAGEO
R111 | 2k | 2k | RES 2K OHM 1% 1/4W 1206 | 1 | RMCF1206FT2K00 | Stackpole Electronics Inc
R121, R411, R412, R413, R414, R502, R503, R506, R512 | 100K | 100K | RES 100K OHM 1% 1/4W 1206 | 9 | RMCF1206FT100K | Stackpole Electronics Inc
R123, R127, R128, R129, R130, R200, R201 | 0R | 0R | RES 0 OHM JUMPER 1/4W 1206 | 7 | RMCF1206ZT0R00 | Stackpole Electronics Inc
R203 | 2.37K | 2.37K | RES 2.37K OHM 1% 1/4W 1206 | 1 | RMCF1206FG2K37 | Stackpole Electronics Inc
R205 | 300 | 300 | RES 300 OHM 1% 1/4W 1206 | 1 | RC1206FR-10300RL | YAGEO
R300, R307 | 459K | 459K | RES 459K OHM 1% 1/4W 1206 | 2 | RN73H2BTTD4593F10 | KOA Speer Electronics, Inc.
R305, R311 | 9.2k, 459k | 9.2k, 459k | RES 9.2K OHM 1% 1/4W 1206 | 2 | RN73H2BTTD9201F10 | KOA Speer Electronics, Inc.
R309 | 1015 | 1015 | RES 1.01K OHM 0.1% 1/3W 1206 | 1 | RNCF1206BTE1K01 | Stackpole Electronics Inc
R314, R315 | 1100 | 1100 | RES 1.1K OHM 1% 1/4W 1206 | 2 | RC1206FR-071K1L | YAGEO
R316, R317 | 21.5k | 21.5k | RES 21.5K OHM 1% 1/4W 1206 | 2 | RC1206FR-0721K5L | YAGEO
R324 | 66.7k | 66.7k | RES 1K OHM 1% 1/4W 1206 | 1 | RC1206FR-0766K5L | YAGEO
R402, R407 | 5k | 5k | RES SMD 5K OHM 1% 0.3W 1206 | 2 | Y16255K00000F9W | Vishay Foil Resistors (Division of Vishay Precision Group)
R403 | 3.3k | 3.3k | RES SMD 3.3K OHM 1% 3/4W 1206 | 1 | CRCW12063K30FKEAHP | Vishay Dale
R404, R408 | 50k | 50k | RES SMD 50K OHM 0.1% 1/4W 1206 | 2 | RT1206BRD0750KL | YAGEO
R415 | 130 | 130 | RES 130 OHM 1% 1/4W 1206 | 1 | RMCF1206FT130R | Stackpole Electronics Inc
R500, R507 | 1.8M | 1.8M | RES 1.8M OHM 1% 1/4W 1206 | 2 | RC1206FR-071M8L | YAGEO
R501, R505, R511 | 3.56K | 3.56K | RES 3.57K OHM 1% 1/4W 1206 | 3 | RC1206FR-073K57L | YAGEO
R504 | 25K | 25K | RES SMD 25K OHM 1% 1/4W 1206 | 1 | Y163025K0000F0W | Vishay Foil Resistors (Division of Vishay Precision Group)
R508 | 8.9K | 8.9K | RES 8.87K OHM 1% 1/4W 1206 | 1 | RC1206FR-078K87L | YAGEO
R510 | 10 | 10 | RES 10 OHM 1% 1/4W 1206 | 1 | RMCF1206FT10R0 | Stackpole Electronics Inc
R514 | 293 | 293 | RES SMD 294 OHM 1% 1/4W 1206 | 1 | CRCW1206294RFKEA | Vishay Dale
TP100, TP101, TP102, TP103, TP104, TP105, TP106, TP107, TP108, TP109, TP110, TP111, TP112, TP113, TP114, TP115, TP200, TP300, TP301, TP302, TP303, TP400, TP401, TP402, TP403, TP404, TP500, TP501, TP502, TP503, TP504, TP505 |  | V_Hist, Vout_osc_HF, GND, Vi_Feed, BHB, AHB, Vi_Error, +2.6V, BHS, BHI/ALI, BLI/AHI, AHS, AHO, BHO, ALO, BLO, +2.5V, Verror1, Verror2, Vcomp_A, Vpos_Ref, Vcomp_D, Vpos_Est_D, Vi_Feed_mean_ADC, Vi_Feed_ADC, Vpos_Ref_ADC, Vpos_Est_A, Vder, Vtst, Vpst, Vi_Feed_LPF, V_I*R | PC TEST POINT MINIATURE RED | 32 | 5000 | Keystone Electronics
U100, U300, U301, U400, U401, U500, U501 |  | MCP664 | IC OPAMP GP 4 CIRCUIT 14TSSOP | 7 | MCP664-E/ST | Microchip Technology
U101 |  | SN74LVC3G06DCUT | IC INVERTER OD 3CH 3-INP 8VSSOP | 1 | SN74LVC3G06DCUT | Texas Instruments
U102 |  | HIP4081A | IC GATE DRVR HALF-BRIDGE 20SOIC | 1 | HIP4081AIBZ | Renesas Electronics America Inc
U103 |  | HO_15-NP-0000 | SENSOR CURRENT HALL 15A AC/DC | 1 | HO 15-NP-0000 | LEM USA Inc.
U104 |  | MCP664 | IC OPAMP GP 4 CIRCUIT 14TSSOP | 1 |  | Microchip Technology
VR100, VR101 | 1k | Trimmer (Thru-Hole) | e, TRIMMER 1K OHM 0.5W PC PIN TOP | 2 | 3299Y-1-102LF | Bourns Inc.
VR200 |  | L78M12CDT-TR | Voltage Regulator | 1 | L78M12CDT-TR | STMicroelectronics
VR201 |  | L78M05CDT-TR | IC REG LINEAR 5V 500MA DPAK | 1 | L78M05CDT-TR | STMicroelectronics
VR202 |  | MAX6071 | IC VREF SERIES 0.08% SOT23-6 | 1 | MAX6071BAUT41+T | Analog Devices Inc./Maxim Integrated
VR500 | 309 | Trimmer (Thru-Hole) | TRIMMER 500 OHM 0.5W PC PIN TOP | 1 | 3299Y-1-501LF | Bourns Inc.

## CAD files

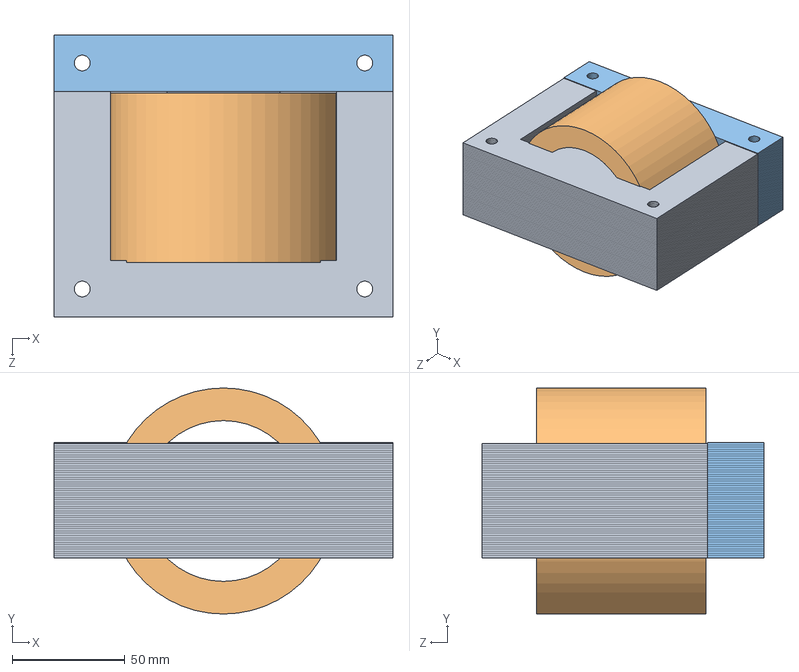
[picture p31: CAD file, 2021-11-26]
SolidWorks/Eleectroiman Completo.SLDASM
150.0 x 100.0 x 125.0 mm
Pieza en forma de E x 51
Carrete y bobinado
Pieza en forma de I x 51

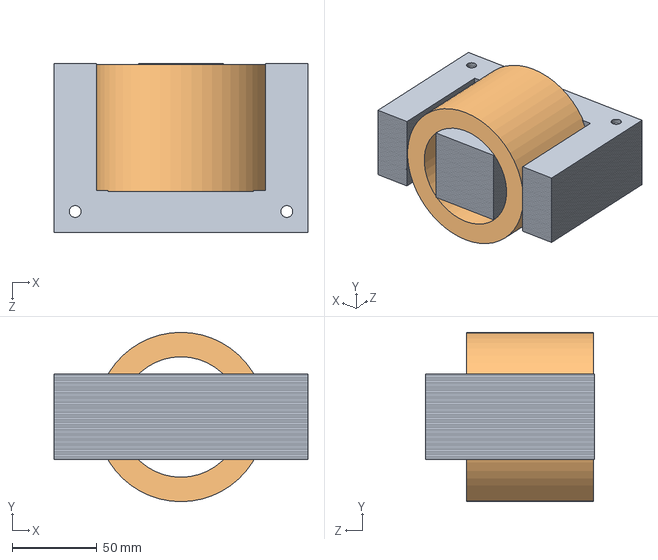
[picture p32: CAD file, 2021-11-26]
SolidWorks/Electroiman Forma de E Completo.SLDASM
150.0 x 100.0 x 100.0 mm
Pieza en forma de E x 51
Carrete y bobinado

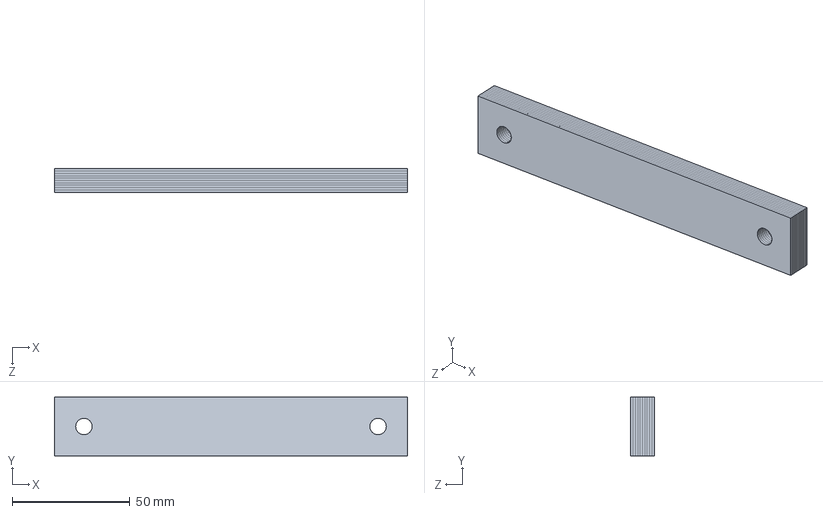
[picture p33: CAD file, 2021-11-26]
SolidWorks/Electroiman Forma de I (10 laminas).SLDASM
150.0 x 25.0 x 10.0 mm
Pieza en forma de I x 10

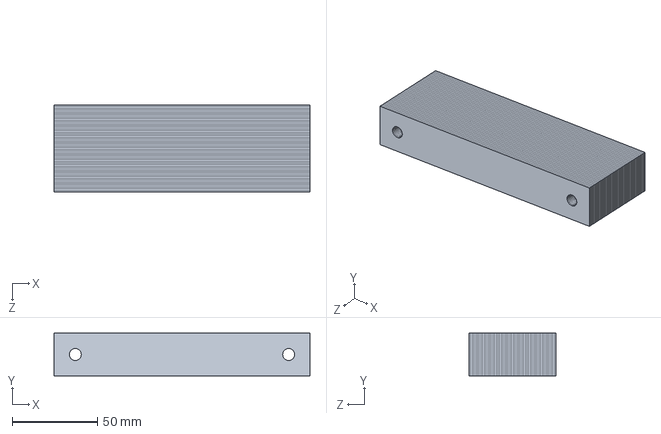
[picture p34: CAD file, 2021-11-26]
SolidWorks/Electroiiman Forma de I Completo.SLDASM
150.0 x 25.0 x 51.0 mm
Pieza en forma de I x 51

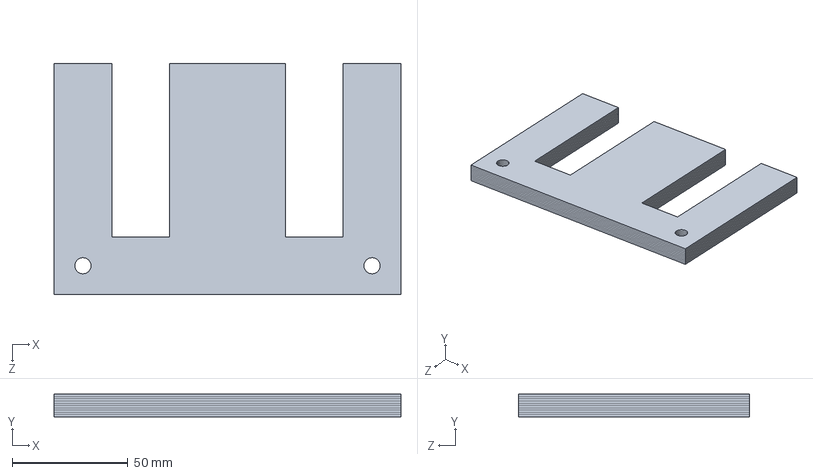
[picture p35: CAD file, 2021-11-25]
SolidWorks/Electroiman Forma de E.SLDASM
150.0 x 9.92 x 100.0 mm
Pieza en forma de E x 10

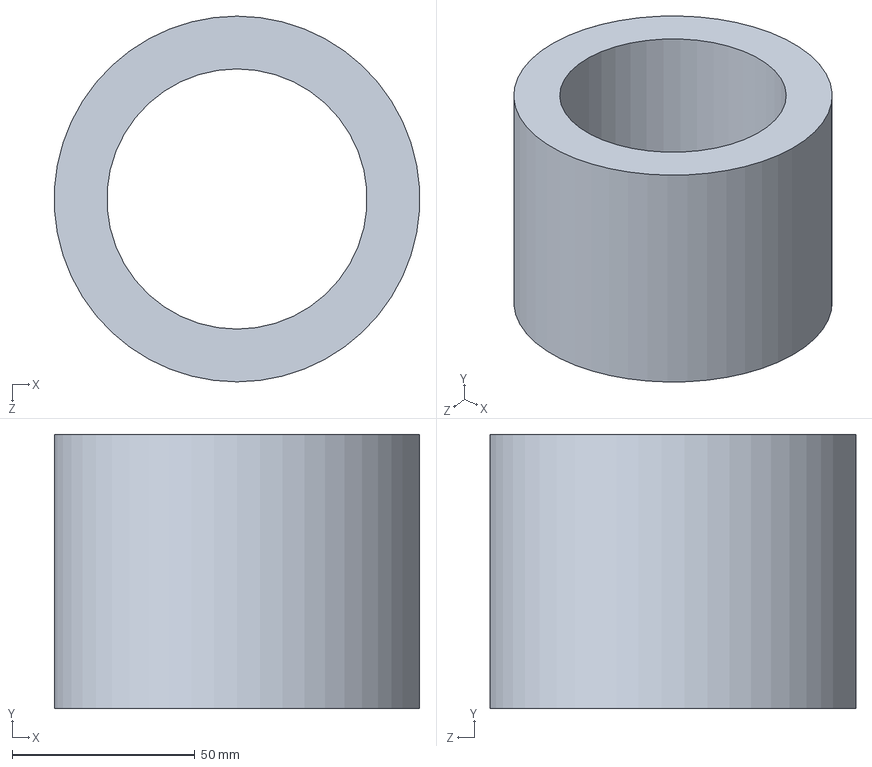
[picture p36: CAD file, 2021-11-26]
SolidWorks/Carrete y bobinado.SLDPRT
99.8 x 75.0 x 100.0 mm

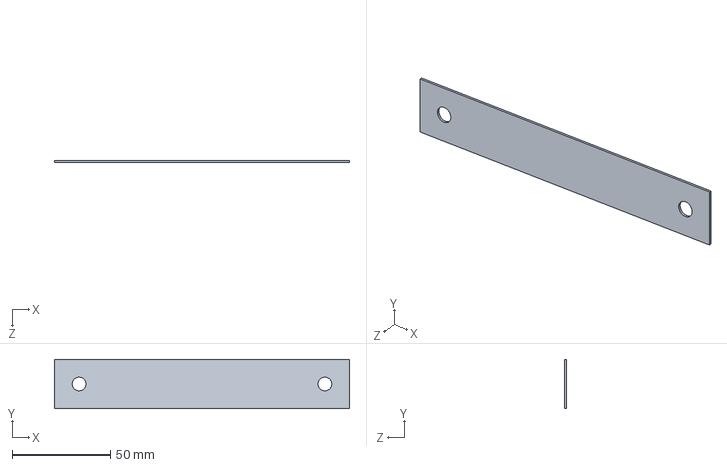
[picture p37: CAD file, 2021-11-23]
SolidWorks/Pieza en forma de I.SLDPRT
150.0 x 25.0 x 1.00 mm

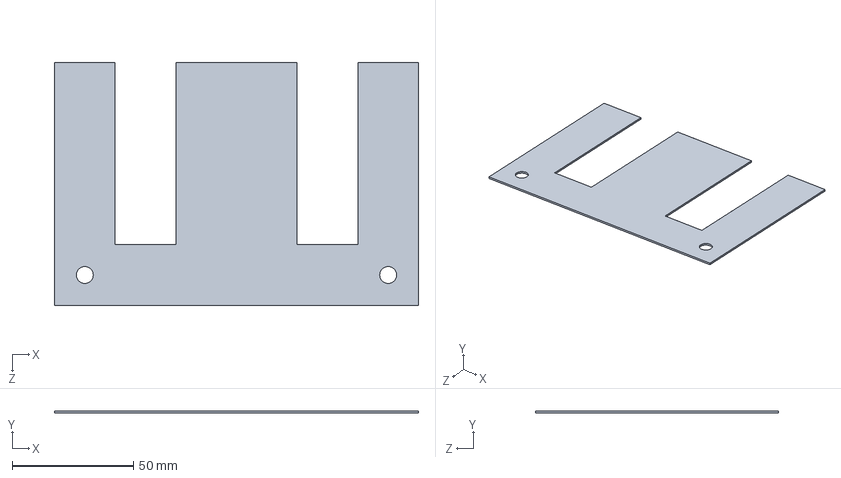
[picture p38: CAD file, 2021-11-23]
SolidWorks/Pieza en forma de E.SLDPRT
150.0 x 1.00 x 100.0 mm

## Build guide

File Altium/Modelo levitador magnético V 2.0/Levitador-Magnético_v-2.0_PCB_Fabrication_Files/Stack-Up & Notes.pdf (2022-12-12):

Layer | Board Layer Stack | Name | Material | Thickness | Constant

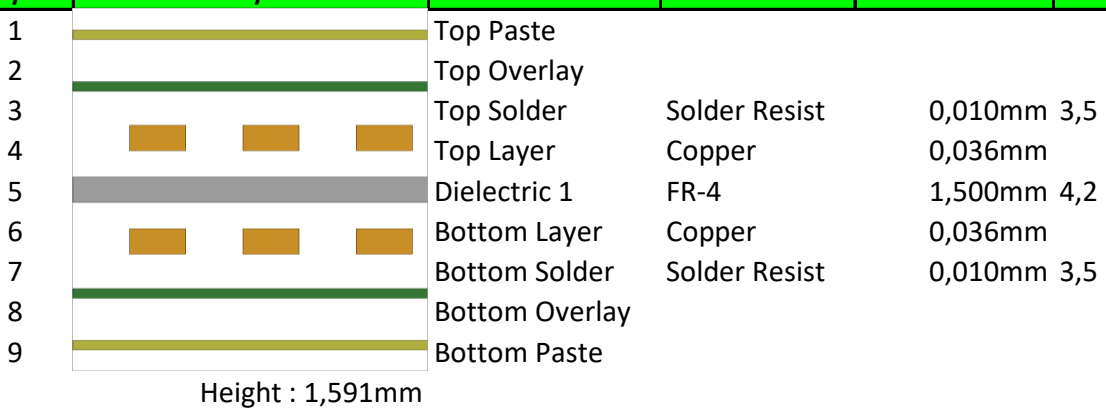
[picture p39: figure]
Top Paste; Top Overlay; Top Solder; Solder Resist; Top Layer; Copper; Dielectric 1; Bottom Layer; Bottom Solder; Bottom Overlay; Bottom Paste; Height : 1,591mm

NOTES

# Board Stack Report

Stack Up | Layer Stack
1. SILKSCREEN: WHITE COLOUR
2. SOLDER MASK: BLACK ON BOTH SIDES

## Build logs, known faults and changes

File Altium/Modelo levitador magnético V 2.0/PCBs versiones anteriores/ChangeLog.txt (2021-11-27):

Version_1: Placement inicial y ruteo de las etapas individuales.
Version_2: Todas las etapas ruteadas

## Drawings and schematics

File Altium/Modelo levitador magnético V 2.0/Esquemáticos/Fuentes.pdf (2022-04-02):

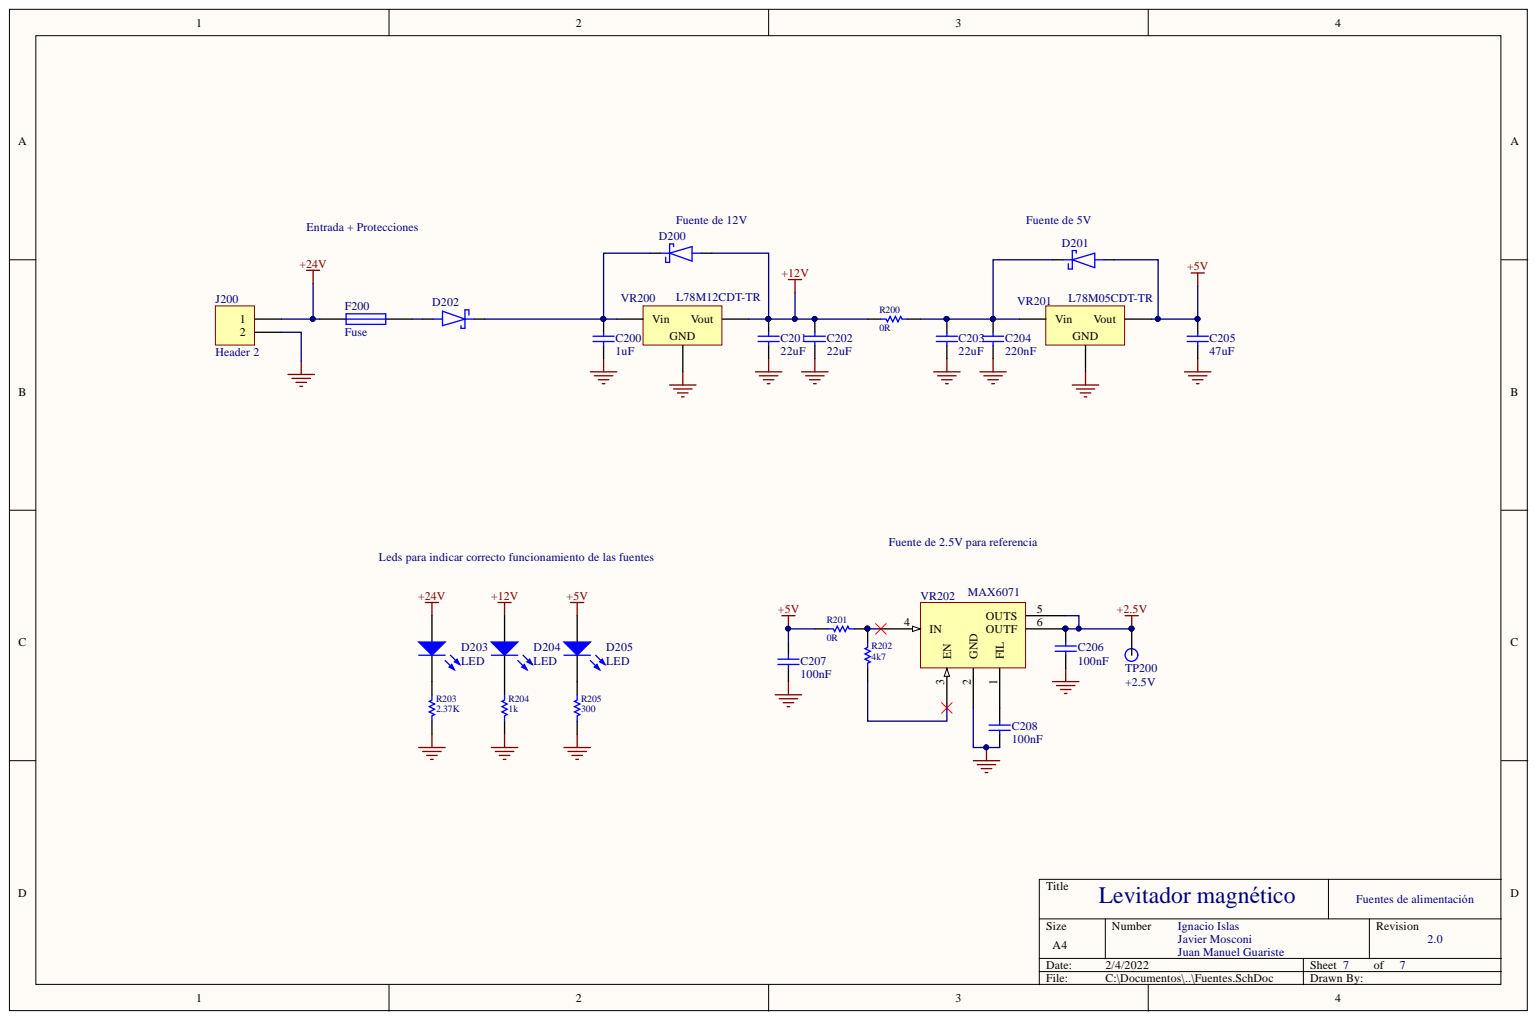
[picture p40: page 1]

Fuente de 2.5V para referencia

Leds para indicar correcto funcionamiento de las fuentes

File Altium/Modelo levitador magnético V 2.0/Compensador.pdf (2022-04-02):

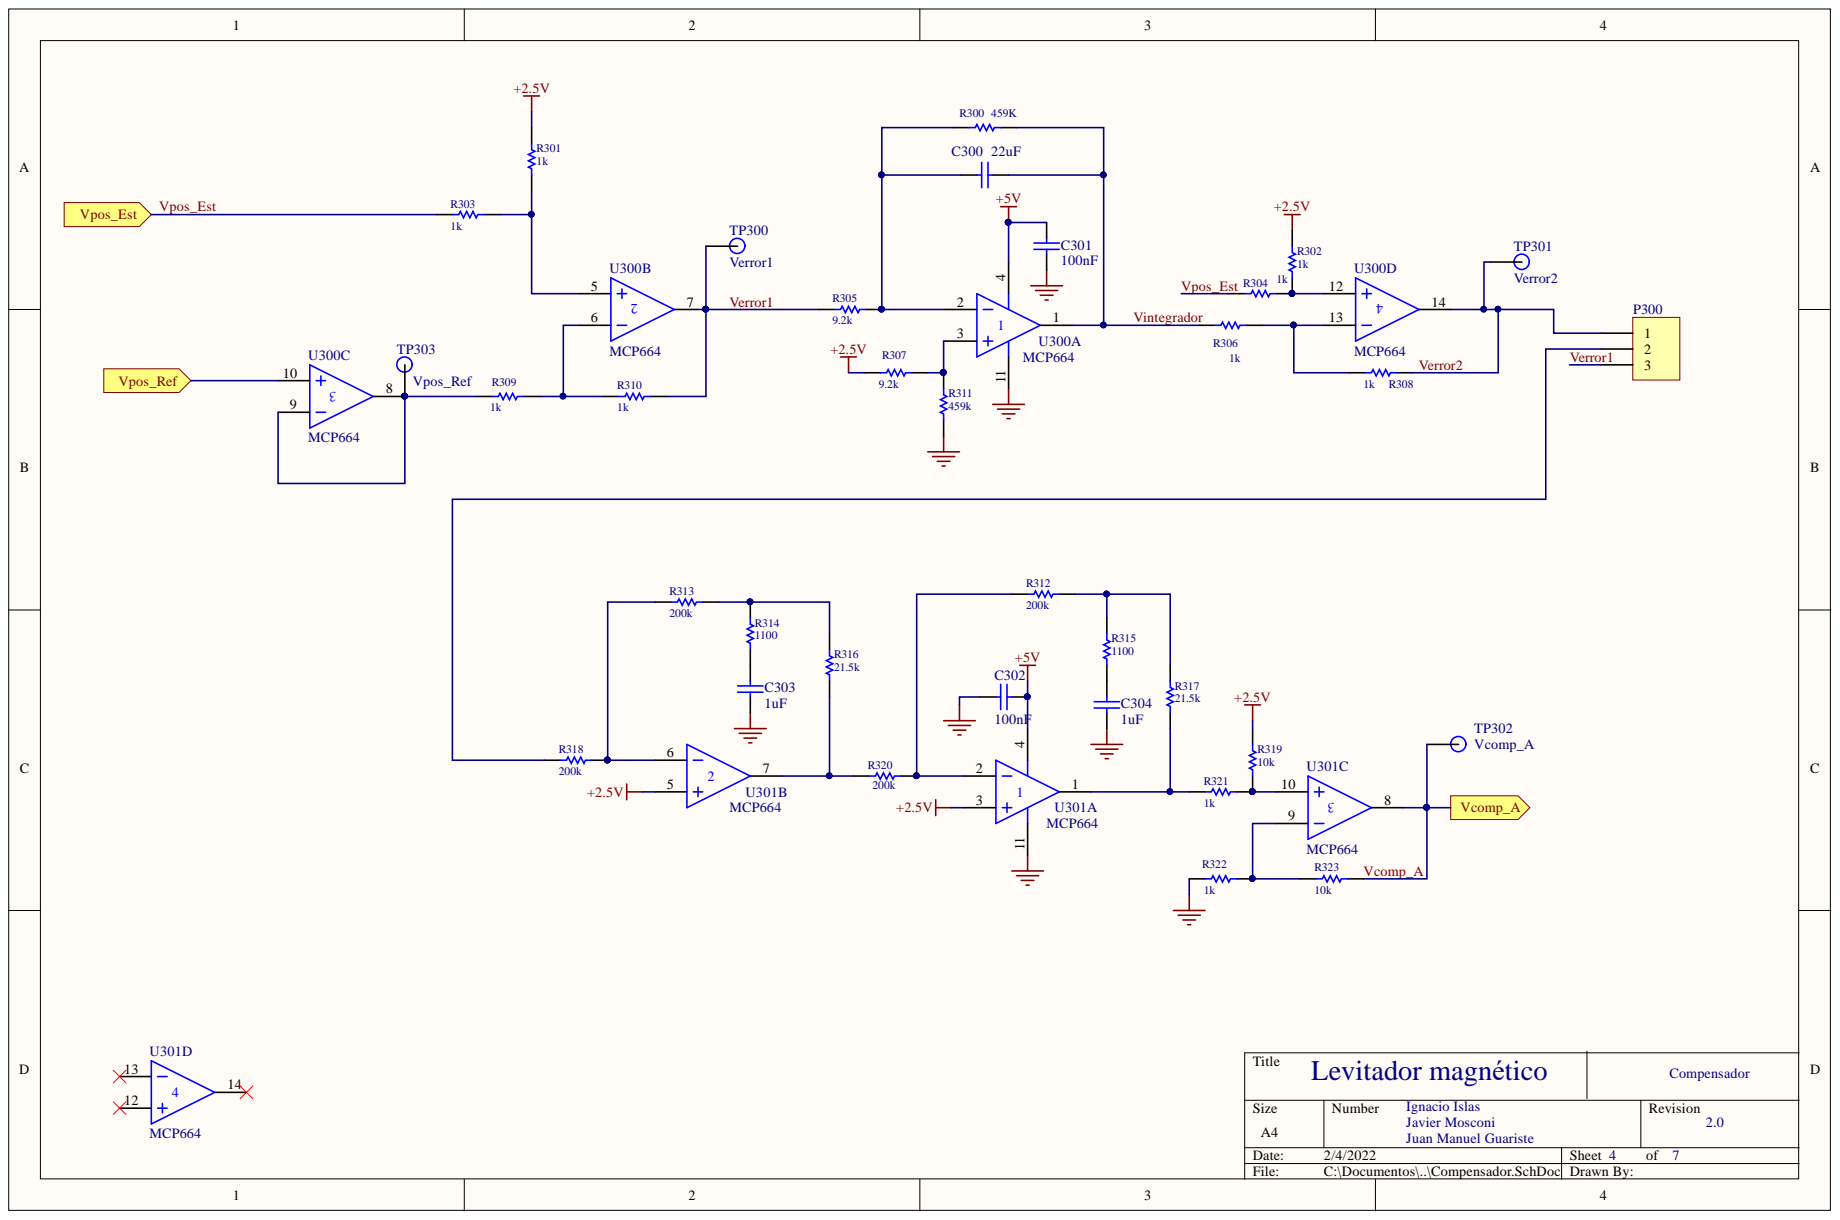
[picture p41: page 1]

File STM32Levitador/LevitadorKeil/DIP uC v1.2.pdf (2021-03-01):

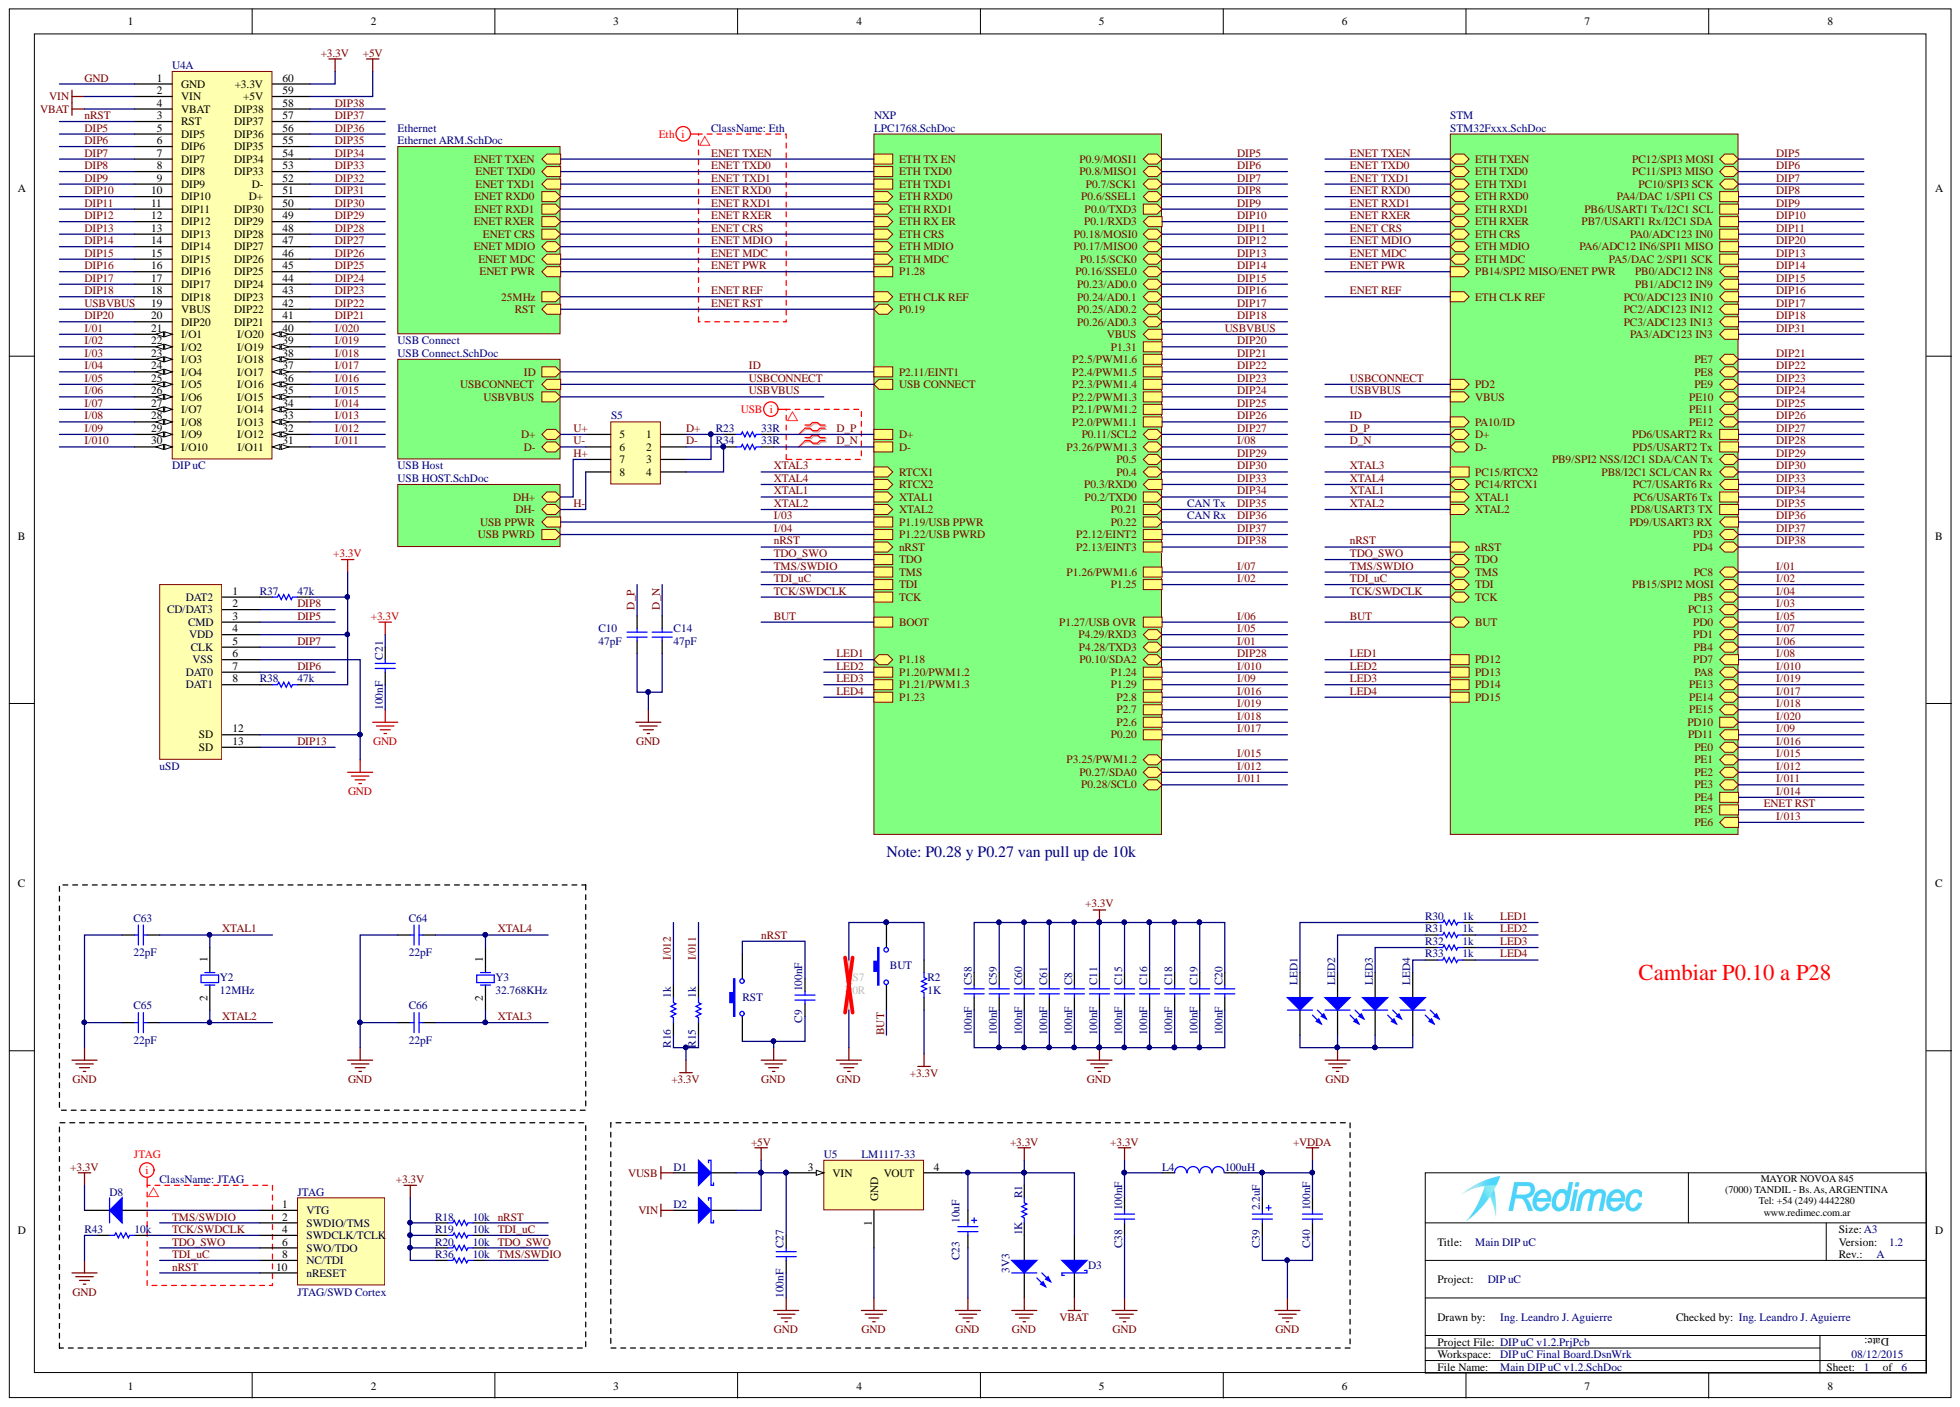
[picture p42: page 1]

DIP11 11 | DIP30 | ENET RXD1 | DIP9
DIP12 12 | DIP29 | ENET RXER | DIP10
DIP13 13 | DIP28 | ENET CRS | DIP11

DIP15 15 | DIP26 | ENET MDC | DIP13
DIP16 16 | DIP25 | ENET PWR | DIP14
DIP17 17 | DIP24 | ENET REF | DIP15

PB9/SPI2 NSS/I2C1 SDA/CAN Tx

Note: P0.28 y P0.27 van pull up de 10k

(7000) TANDIL - Bs. As, ARGENTINA

Tel: +54 (249) 4442280
www.redimec.com.ar

DIP uC v1.2.PrjPcb
DIP uC Final Board.DsnWrk
Main DIP uC v1.2.SchDoc

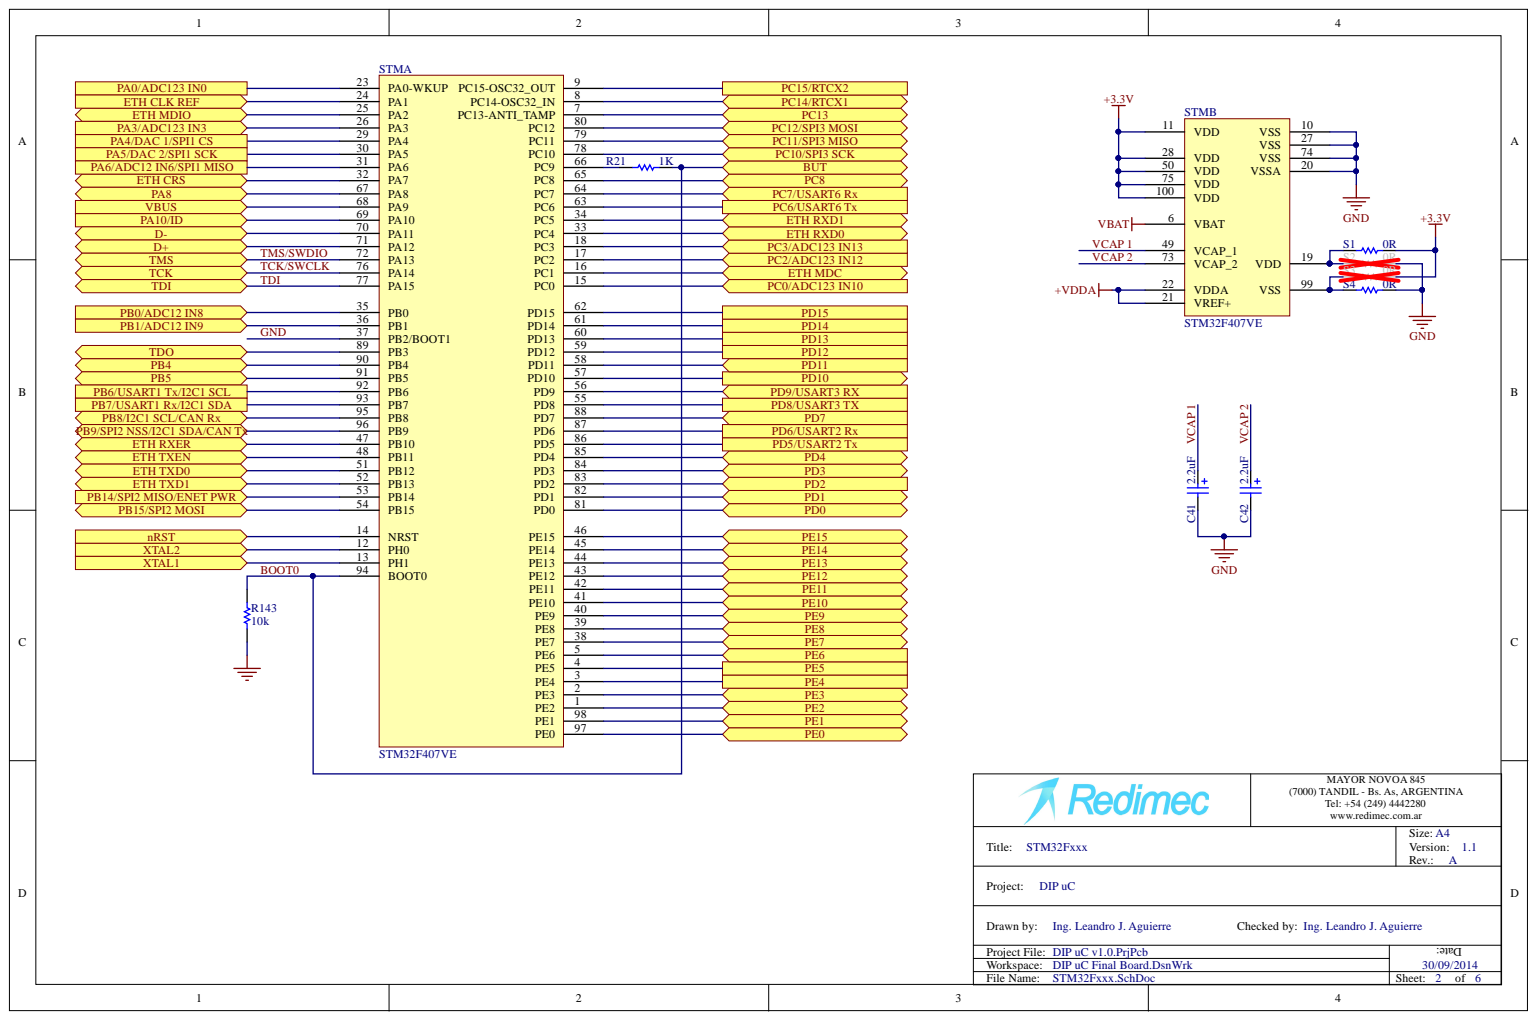
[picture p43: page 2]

6 9 | 34 3 PC5
7 0 | 3 | 4 9 7 3

9 3 | 5
9 5

M AY OR N O V O A 845 (7000) T A N DIL - Bs. A s, ARG E N TIN A Te l : +54 (249) 4442280 w w w.redi m e c.com.a r

T i t le: STM3 2Fx x x | Size: A 4 Vers i o n : 1.1 Rev.: A

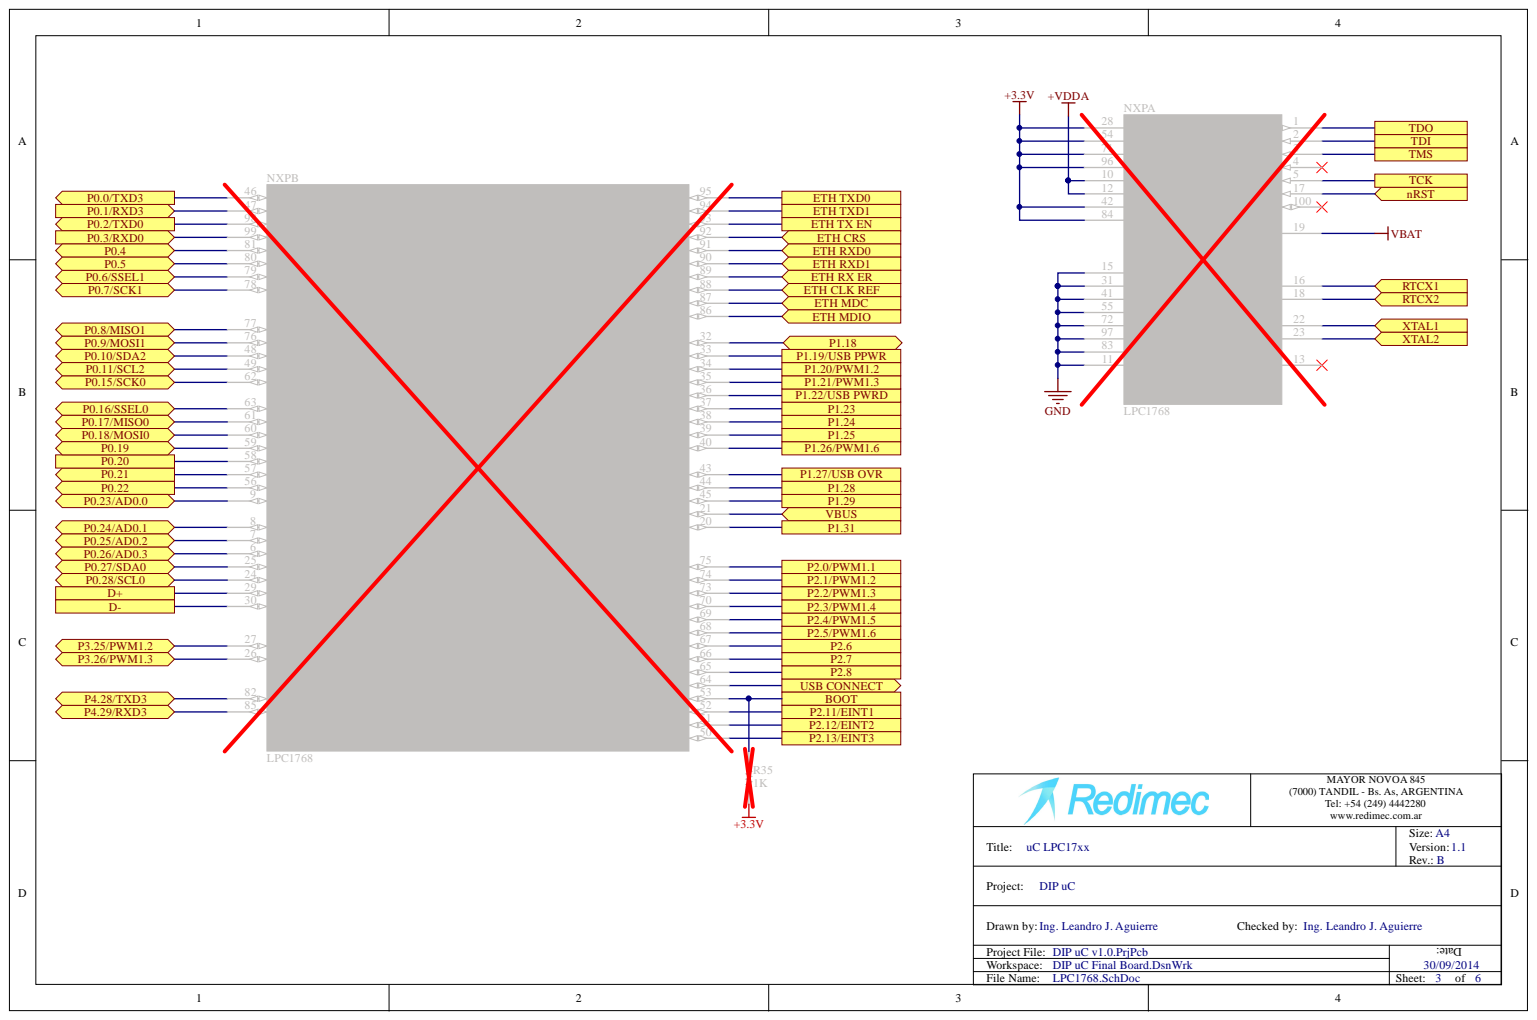
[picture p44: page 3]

5 4 | 2
7 1 | 3
9 6
1 0
1 2

TCK TMS TDI TDO

5 2
5 1
5 0

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

T i t le: uC LPC1 7 x x | Size: A 4 Vers i o n : 1.1 Rev.: B

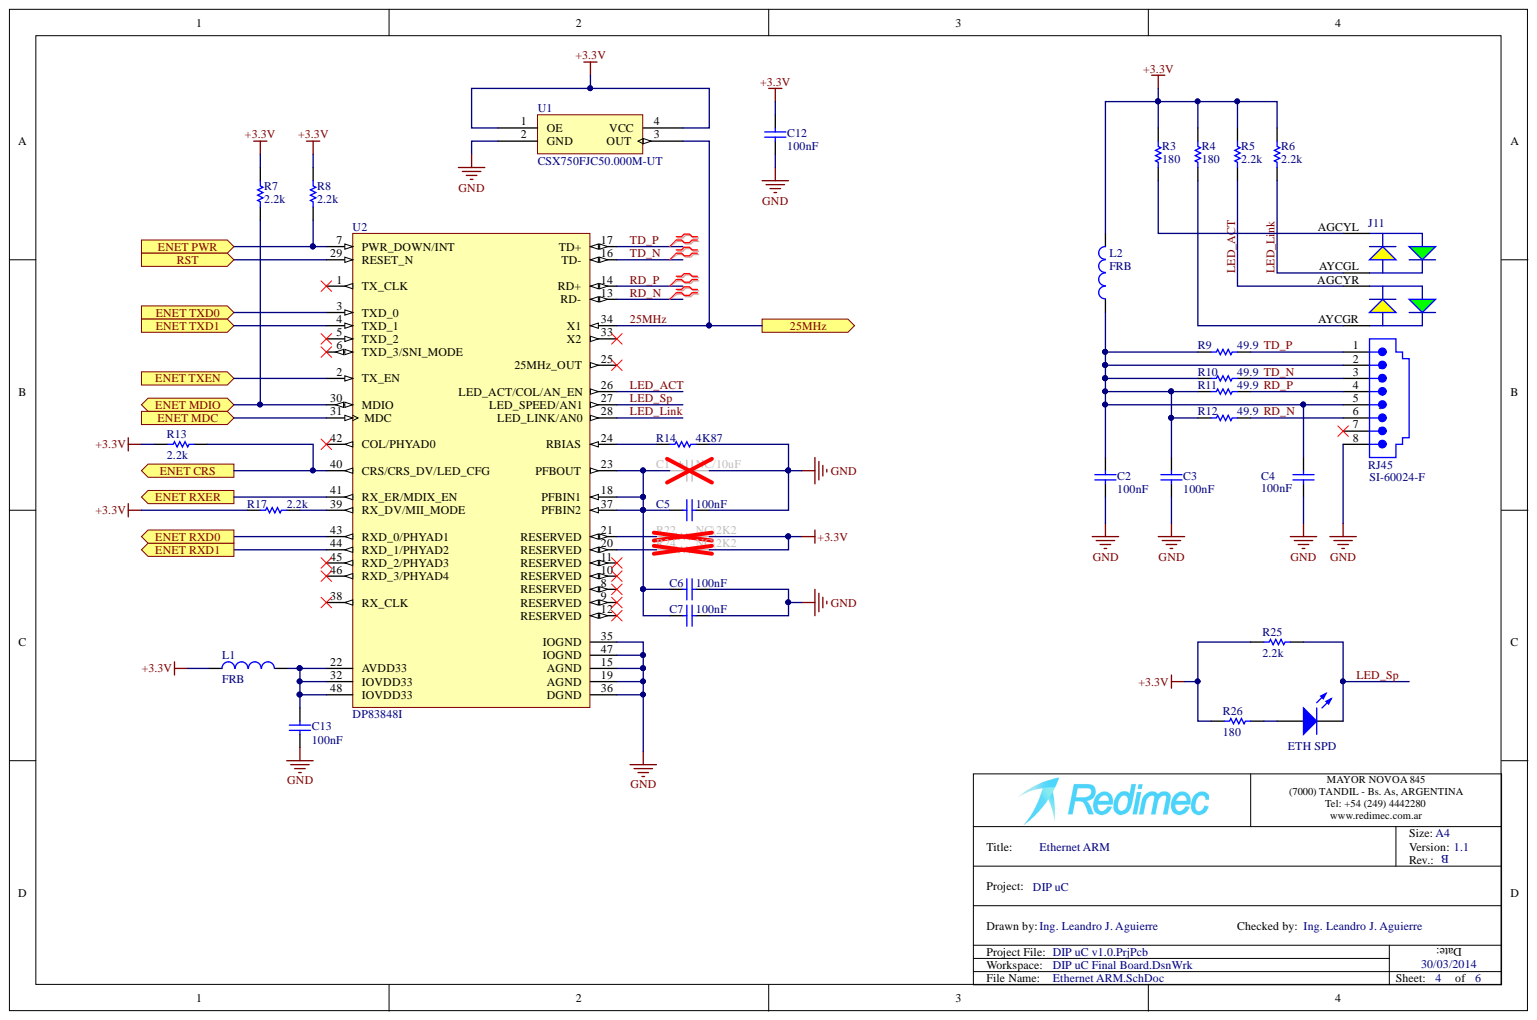
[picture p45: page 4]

4 7
1 5

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

T i t le: E t hernet ARM | Size: A 4 Vers i o n : 1.1 Rev.:

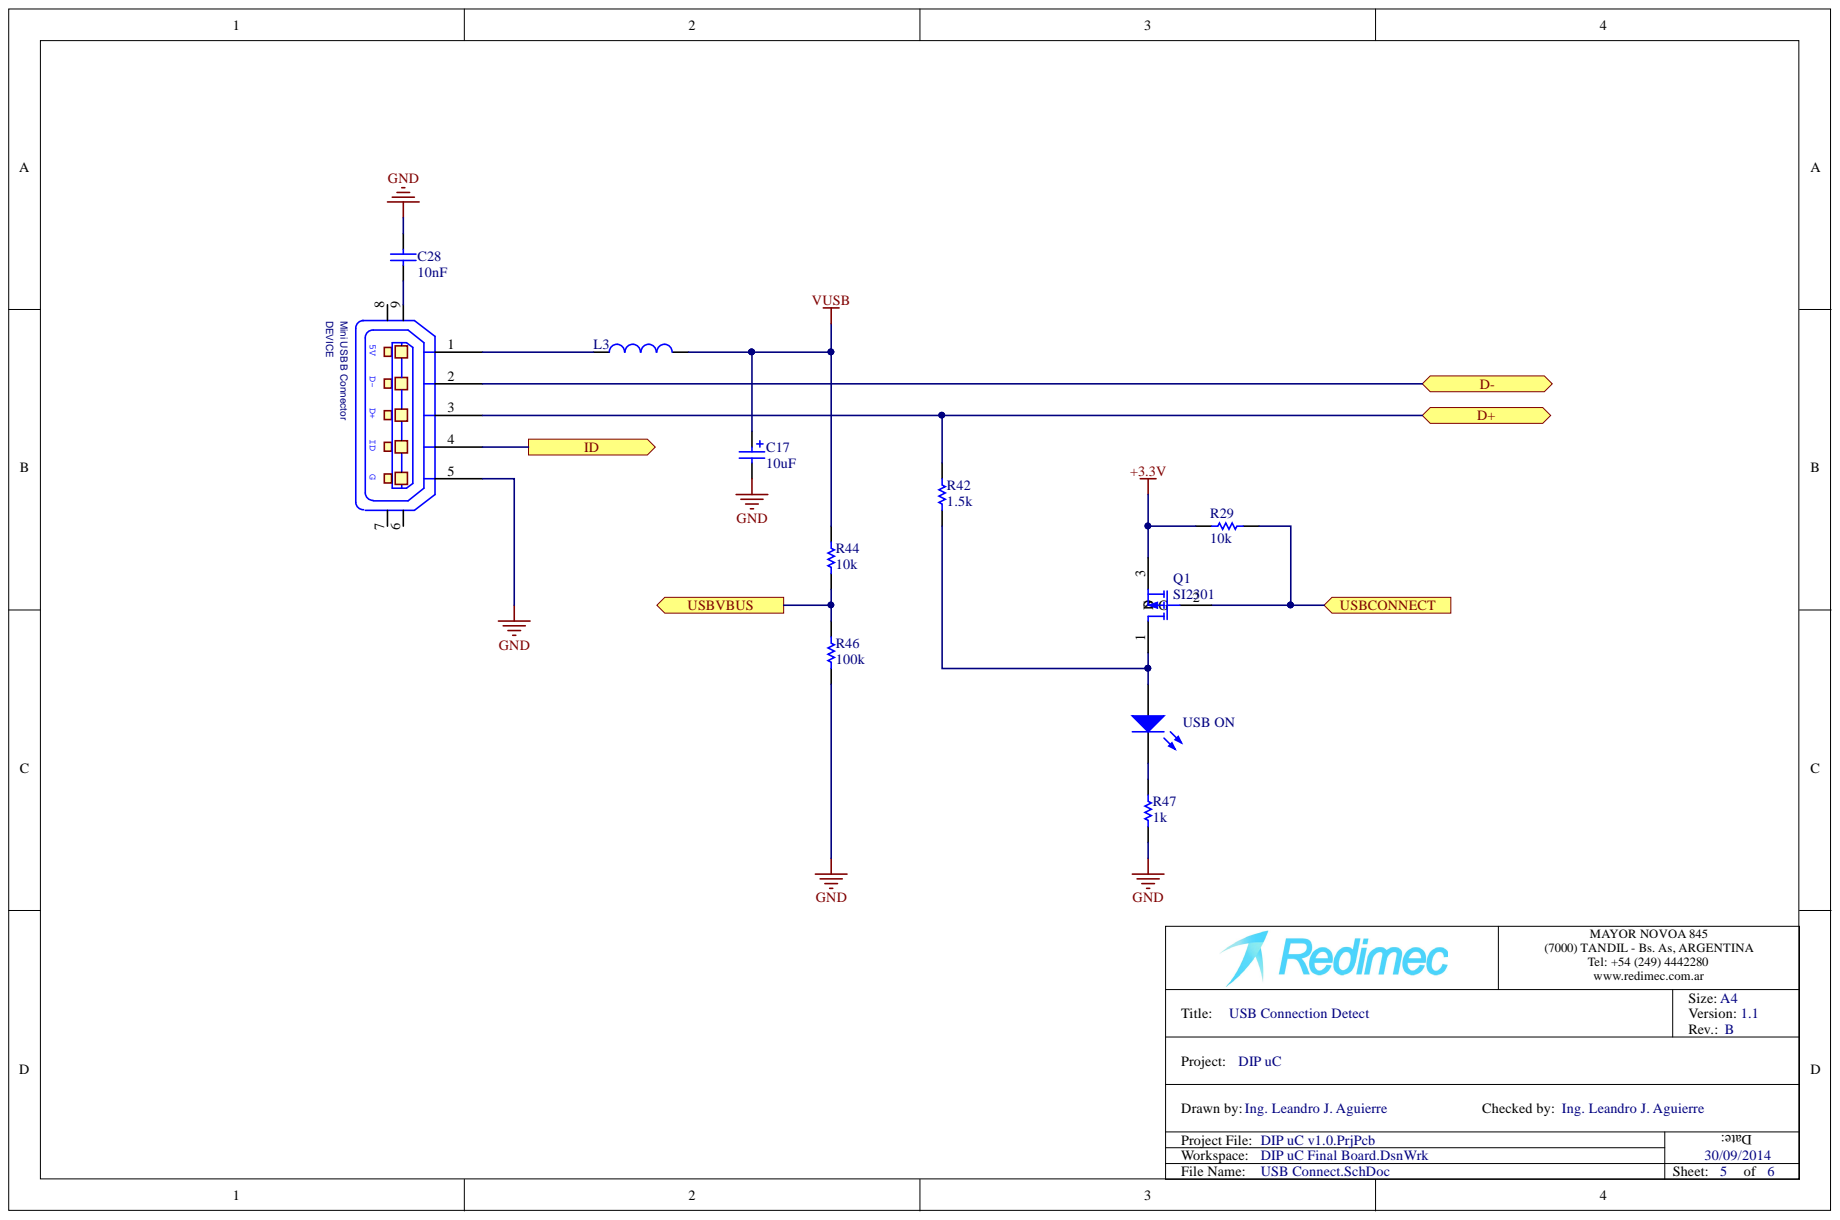
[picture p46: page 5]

MAYOR NOVOA 845 (7000) TANDIL - Bs. As, ARGENTINA Tel: +54 (249) 4442280 www.redimec.com.ar

Title: USB Connection Detect | Size: A4 Version: 1.1 Rev.: B

DIP uC v1.0.PrjPcb
DIP uC Final Board.DsnWrk
USB Connect.SchDoc

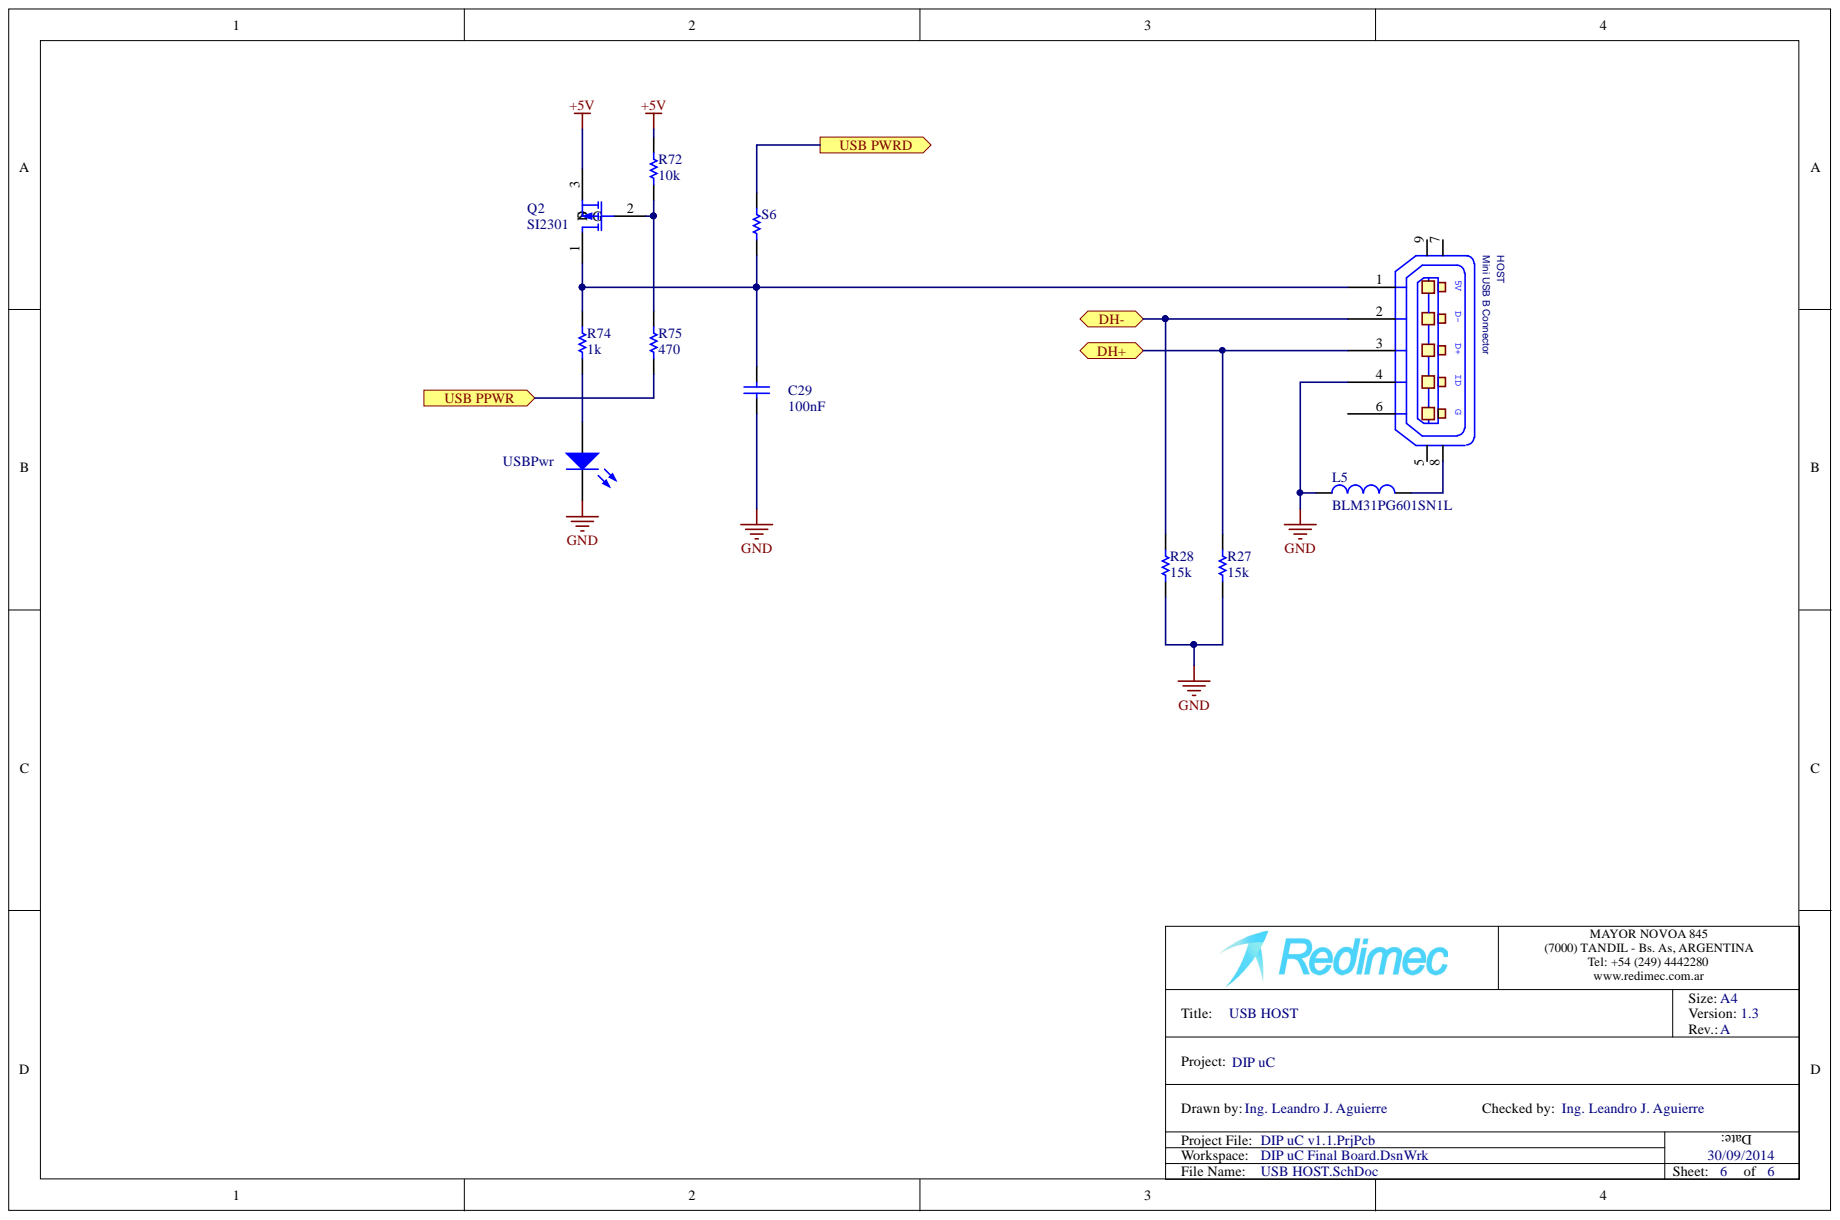
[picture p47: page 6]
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

T i t le: USB H OST | Size: A 4 Vers i o n : 1.3 Rev.: A


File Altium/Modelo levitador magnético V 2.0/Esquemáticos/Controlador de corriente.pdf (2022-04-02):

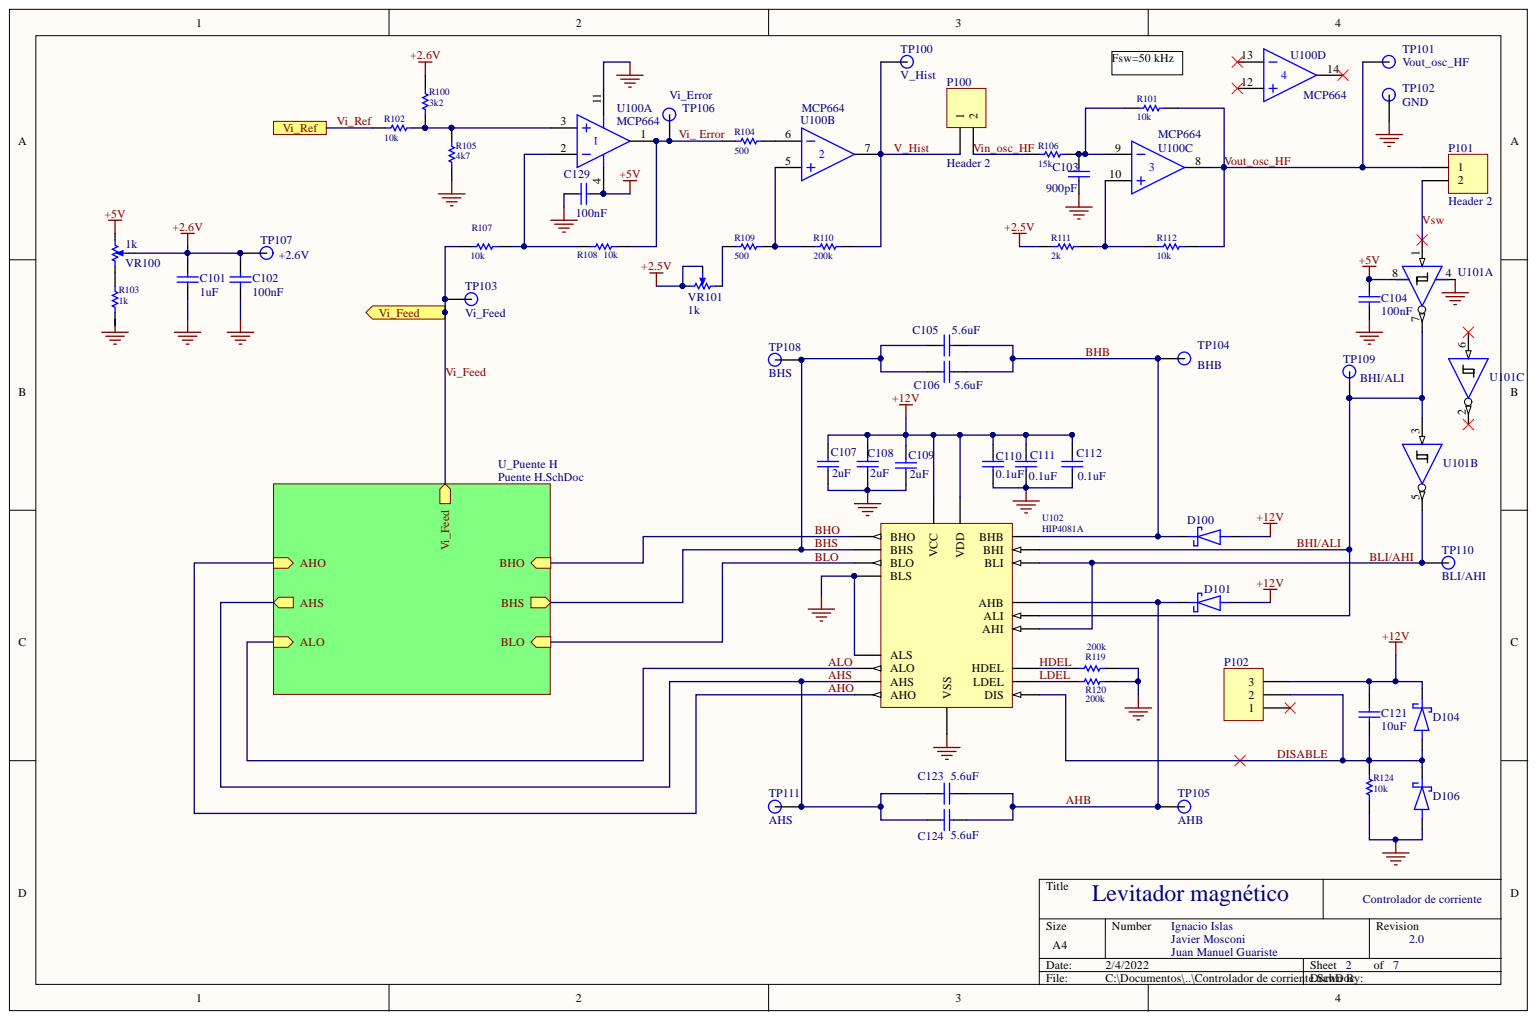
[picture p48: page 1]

BHS
BLO

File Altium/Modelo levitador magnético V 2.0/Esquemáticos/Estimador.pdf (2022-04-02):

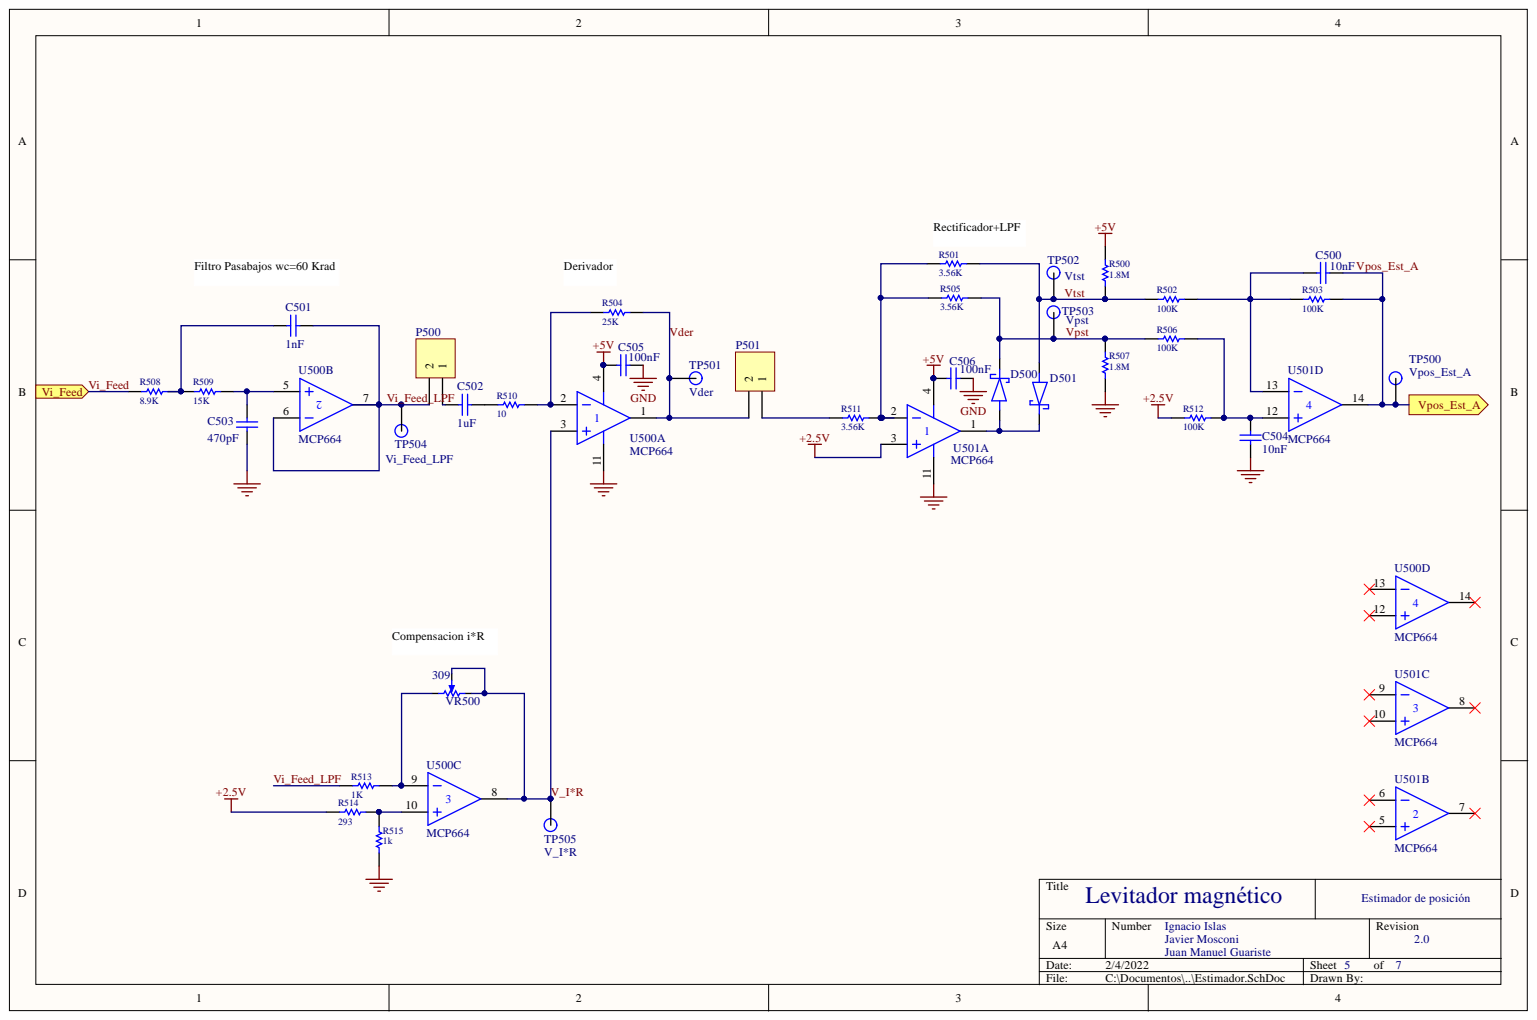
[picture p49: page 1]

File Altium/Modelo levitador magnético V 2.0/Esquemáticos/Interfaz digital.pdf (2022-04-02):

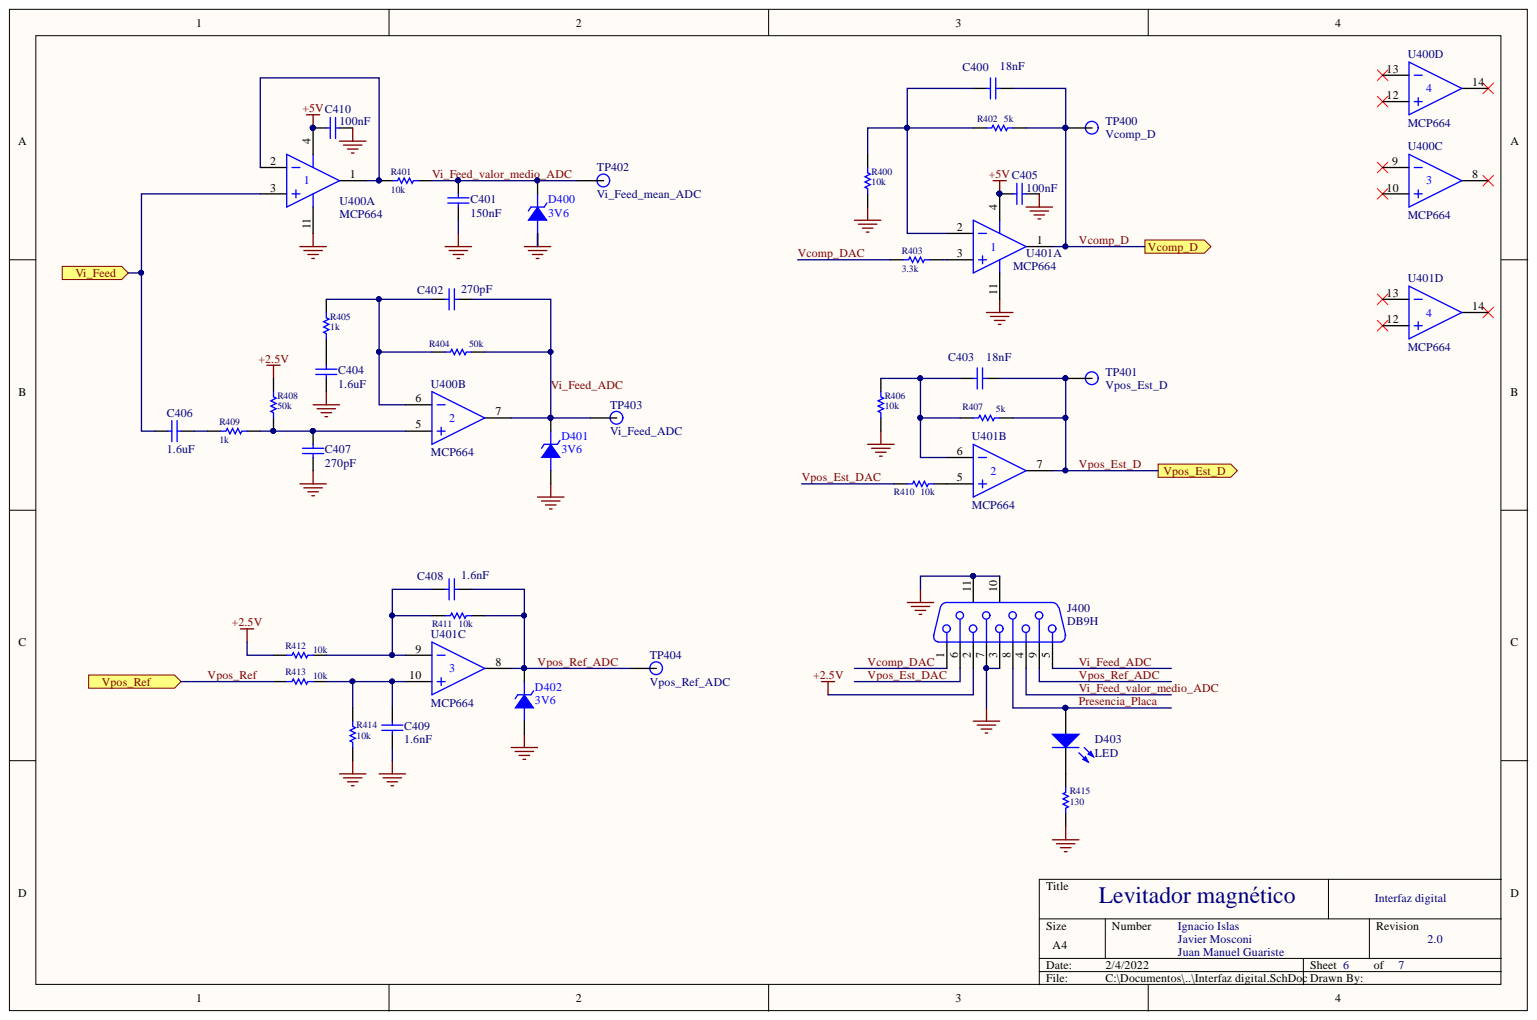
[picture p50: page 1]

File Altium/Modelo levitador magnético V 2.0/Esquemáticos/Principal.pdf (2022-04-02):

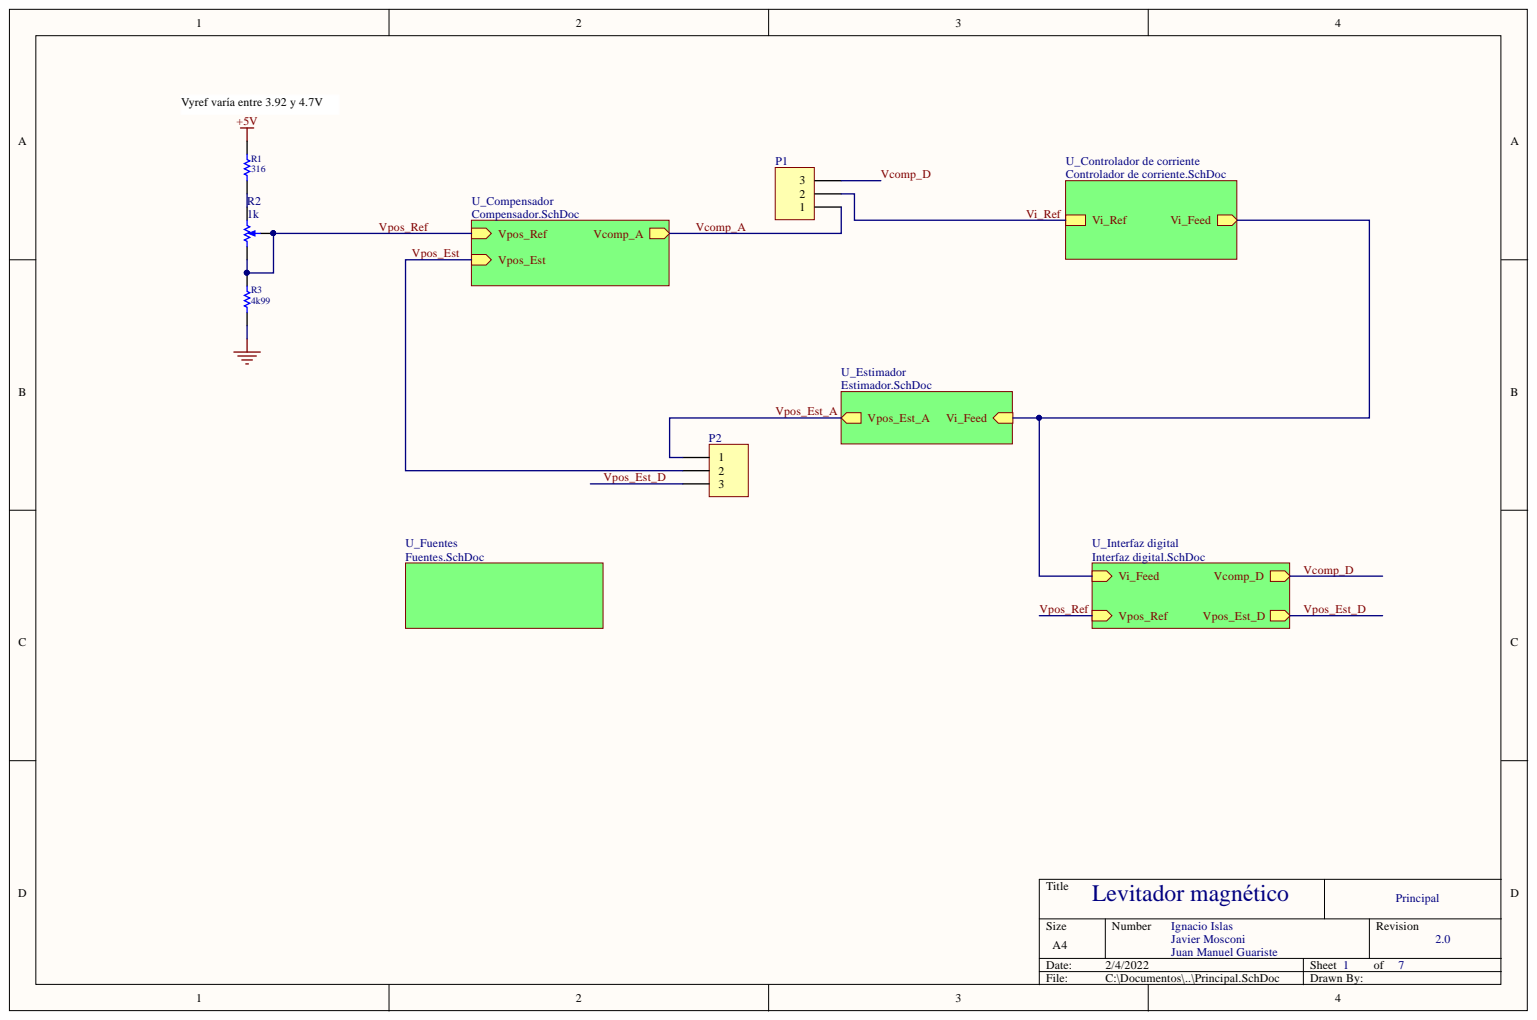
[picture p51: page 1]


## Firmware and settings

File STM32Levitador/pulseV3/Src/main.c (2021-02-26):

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
/* Includes ------------------------------------------------------------------*/
#include "main.h"
#include "cmsis_os.h"

/* USER CODE BEGIN Includes */
#include "hamamatsu.h"
#include "hamamatsu.c"
#include "comm_protocol.h"
#include "comm_protocol.c"
#include <stdlib.h>
#include <time.h>
#include <string.h>
#include <math.h>
/* USER CODE END Includes */

/* USER CODE BEGIN PD */
#define ITM_Port8(n)    (*((volatile unsigned char *)(0xE0000000+4*n)))
#define ITM_Port16(n)   (*((volatile unsigned short*)(0xE0000000+4*n)))
#define ITM_Port32(n)   (*((volatile unsigned long *)(0xE0000000+4*n)))

#define DEMCR           (*((volatile unsigned long *)(0xE000EDFC)))
#define TRCENA          0x01000000
/* USER CODE END PD */

ADC_HandleTypeDef hadc1;

DAC_HandleTypeDef hdac;

TIM_HandleTypeDef htim2;
TIM_HandleTypeDef htim4;
TIM_HandleTypeDef htim5;

UART_HandleTypeDef huart5;
UART_HandleTypeDef huart3;
UART_HandleTypeDef huart6;
DMA_HandleTypeDef hdma_uart5_rx;
DMA_HandleTypeDef hdma_usart3_rx;
DMA_HandleTypeDef hdma_usart6_rx;

osThreadId defaultTaskHandle;
osThreadId RxTaskHandle;
/* USER CODE BEGIN PV */
uint8_t new_char; 			//UART6 DMA
uint8_t new_char_uart3; //UART3 DMA
uint8_t new_char_uart5; //UART5 DMA

uint8_t uart3_buffer[64]; //buffer hv1
uint8_t uart3_buffer_index;

uint8_t uart5_buffer[64]; //buffer hv2
uint8_t uart5_buffer_index;

command_t command_input; 

uint32_t	PMT2_count_vv = 0;
uint32_t	PMT1_count_hh = 0;
uint32_t	PMT2_count_hv = 0;
uint32_t	PMT1_count_vh = 0;

uint32_t lv_h_prom = 0;
uint32_t lv_v_prom = 0;
uint32_t lh_h_prom = 0;
uint32_t lh_v_prom = 0;

float pol;
volatile uint16_t tim4_overflow;
volatile uint16_t tim5_overflow;
volatile bool counting = false;
uint8_t uart_tx_buffer[128];

float led_lvl;

float aux2;
uint16_t conversion;

uint16_t n = 50;	// cantidad de muestas
uint16_t dt = 20; 	//tiempo led on(Ventana)
uint8_t t_off = 10;//tiempo led off

bool record=0;
uint16_t debAux=0;

struct
{
	uint32_t lv_v_zero; //zero para canal V (Exitación V)
	uint32_t lv_h_zero; //zero para canal H (Exitación V)
	uint32_t lh_v_zero; //zero para canal V (Exitación H)
	uint32_t lh_h_zero;	//zero para canal h (Exitación H)
	float rv;
	float rh;
	float rv_rh;
	float pol;
	float g_factor;
	uint16_t led1_power;
	uint16_t led2_power;
	bool measuring;
	uint16_t 	hv1_power;
	uint16_t	hv2_power;
}polarimeter;

struct __FILE { int handle; /* Add whatever you need here */ };
FILE __stdout;
FILE __stdin;

/* USER CODE END PV */

void SystemClock_Config(void);
static void MX_GPIO_Init(void);
static void MX_DMA_Init(void);
static void MX_ADC1_Init(void);
static void MX_DAC_Init(void);
static void MX_TIM4_Init(void);
static void MX_TIM5_Init(void);
static void MX_TIM2_Init(void);
static void MX_UART5_Init(void);
static void MX_USART3_UART_Init(void);
static void MX_USART6_UART_Init(void);
void StartDefaultTask(void const * argument);
void RXTaskHandler(void const * argument);

/* USER CODE BEGIN 0 */

static float calc_polarization(uint32_t lv_count_h, uint32_t lv_count_v,uint32_t lh_count_h, uint32_t lh_count_v)
/**
       * Funcion devuelve el Calculo de la polarizacion.
       * @param rv an float argument.
       * @param rh a float argument.
       * @return The polarization value.
       */
{
	//if (lv_count_h <1 || lh_count_h <1 ) ESPERAR LA OTRA FUENTE
		//{return 0;}
	float rv = (float) lv_count_v/lv_count_h;
	float rh = (float) lh_count_v/lh_count_h;

	//if (rh == 0.0)
		//{return 0;}

	float rv_rh =  rv/rh;

	polarimeter.rv = rv;
	polarimeter.rh = rh;
	polarimeter.rv_rh = rv_rh;
	polarimeter.pol = (rv_rh-1)/(rv_rh+2);
		
	return (rv_rh-1)/(rv_rh+2);
}

int fputc(int ch, FILE *f) {
  if (DEMCR & TRCENA) {
    while (ITM_Port32(0) == 0);
    ITM_Port8(0) = ch;
  }
  return(ch);
}

float measure(uint16_t n, uint16_t dt, uint16_t t_off)
/**
			 * @description: Funcion que realiza el Conteo de Pulsos
       * @params: n = cantidad de muestras, dt: tiempo de conteo con leds on, toff: tiempos muertos
       */
/************************************************
 *  CONFIGURACIÓN CANALES
		LED 1 (DAC_CHANNEL_1) --> Exitación horizontal
		LED 2 (DAC_CHANNEL_2) --> Exitación vertical
		Canal horizontal: canal1 - htim4
		Canal vertical: canal2 - htim5
 ***********************************************/
{
	uint8_t btnSts= HAL_GPIO_ReadPin(GPIOA, COVER_Pin);
	if(btnSts==0){
	
		PMT1_count_vh=0;
		PMT1_count_hh=0;
		PMT2_count_hv=0;
		PMT2_count_vv=0;
		lv_h_prom = 0;
		lv_v_prom = 0;
		lh_h_prom = 0;
		lh_v_prom = 0;
		
		polarimeter.measuring = true;
		
		if (polarimeter.hv1_power==0 & polarimeter.hv2_power==0){
			hps_sendcmd(&huart3, HBV,(uint8_t*)"7B70", 4); //!Tension en 56V, definida para el pmt1 
			hps_sendcmd(&huart5, HBV,(uint8_t*)"7B70", 4); //!Tension en 56V, definida para el pmt2 
		} 
		for (uint16_t r = 0; r < 5;r++)
		{
			hps_sendcmd(&huart3, HON,NULL, 0); 	// Enciendo pmt1 
			HAL_Delay(10);
			hps_sendcmd(&huart5, HON,NULL, 0);	// Enciendo pmt2
			
		}	
		HAL_Delay(1000);
		if(polarimeter.led1_power==0){
			polarimeter.led1_power=4095;
		}
		if(polarimeter.led2_power==0){
				polarimeter.led2_power=4095;
		}
		
		for (uint16_t i = 0; i < n;i++)
		{
			//!CANAL 1
			
			//!Mido exitando con led horizontal (DAC 1)
			HAL_DAC_SetValue(&hdac, DAC_CHANNEL_2, DAC_ALIGN_12B_R,0);
			HAL_DAC_SetValue(&hdac, DAC_CHANNEL_1, DAC_ALIGN_12B_R,polarimeter.led1_power);
			//HAL_DAC_SetValue(&hdac, DAC_CHANNEL_1, DAC_ALIGN_12B_R,0);
			osDelay(t_off);
			//Enciendo Contadores
			HAL_TIM_Base_Start_IT(&htim4);
			HAL_TIM_Base_Start_IT(&htim5);
			//!Reinicio contadores y cuento en ventana con duracion dt
			tim4_overflow = 0;
			tim5_overflow = 0;
			__HAL_TIM_SetCounter(&htim4,0);
			__HAL_TIM_SetCounter(&htim5,0);
			osDelay(dt);
			//!Paro los contadores y guardo los valores
			HAL_TIM_Base_Stop_IT(&htim4);
			HAL_TIM_Base_Stop_IT(&htim5);
			PMT1_count_hh = __HAL_TIM_GetCounter(&htim4) + tim4_overflow * 65535;
			PMT2_count_hv = __HAL_TIM_GetCounter(&htim5) + tim5_overflow * 65535; 
			
			if (polarimeter.g_factor > 0)
				PMT2_count_hv *= polarimeter.g_factor; //!corrijo diferencia entre canales
			
			lh_h_prom += PMT1_count_hh;
			lh_v_prom += PMT2_count_hv;
			
			//!Canal2
			
			//! Mido exitando con led vertical (DAC 2)
			HAL_DAC_SetValue(&hdac, DAC_CHANNEL_2, DAC_ALIGN_12B_R,polarimeter.led2_power);
			//HAL_DAC_SetValue(&hdac, DAC_CHANNEL_2, DAC_ALIGN_12B_R,0);
			HAL_DAC_SetValue(&hdac, DAC_CHANNEL_1, DAC_ALIGN_12B_R,0);
			osDelay(t_off);
			
			//! Enciendo Contadores
			HAL_TIM_Base_Start_IT(&htim4);
			HAL_TIM_Base_Start_IT(&htim5);
			
			//! Reinicio contadores y cuento en ventana con duracion dt
			tim4_overflow = 0;
			tim5_overflow = 0;
			__HAL_TIM_SetCounter(&htim4,0);
			__HAL_TIM_SetCounter(&htim5,0);
			osDelay(dt);
			
			//!Paro los contadores y guardo los valores
			HAL_TIM_Base_Stop_IT(&htim4);
			HAL_TIM_Base_Stop_IT(&htim5);
			PMT1_count_vh = __HAL_TIM_GetCounter(&htim4) + tim4_overflow * 65535;
			PMT2_count_vv = __HAL_TIM_GetCounter(&htim5) + tim5_overflow * 65535; 
			
			if (polarimeter.g_factor > 0)
				PMT2_count_vv *= polarimeter.g_factor; //!corrijo diferencia entre canales
			
			lv_h_prom += PMT1_count_vh;
			lv_v_prom += PMT2_count_vv;
			
			record=1; //Para DEBUG
			osDelay(100);
			record=0; //Para debug
			debAux++;
			
		}
		//!Apago Fuentes
		hps_sendcmd(&huart3, HOF,NULL, 0); //!Desactiva salida de tension
		hps_sendcmd(&huart5, HOF,NULL, 0); //!Desactiva salida de tension
		//!Apago Leds
		HAL_DAC_SetValue(&hdac, DAC_CHANNEL_1, DAC_ALIGN_12B_R,0);
		HAL_DAC_SetValue(&hdac, DAC_CHANNEL_2, DAC_ALIGN_12B_R,0);
		//! Calculo promedios
		
		lv_h_prom /= n;
		lv_v_prom /= n;
		lh_h_prom /= n;
		lh_v_prom /= n;

		/*!Asignacion de Los conteos de Pulos a la estructura Polarimeter
		!*/

			polarimeter.lv_h_zero = lv_h_prom;
			polarimeter.lv_v_zero = lv_v_prom;
			polarimeter.lh_h_zero = lh_h_prom;
			polarimeter.lh_v_zero = lh_v_prom;

		polarimeter.measuring = false;
	}else if(btnSts==1){
		//uint8_t res[14]="$$RCOVER,1\r\n";
		//HAL_UART_Transmit(&huart6,res,sizeof(res),100);
		command_input.name=CMD_NULL;
	}
}

void data(command_t new_cmd)
/**
*@description: Accion a partir del comando recibido
*@description: Todos los comandos son de la siguiente forma: "$(Commando),valor1,valor2,valor3/r/n/n"
*@description: La respuesta si el comando fue recibido es la siguiente: "$(Commando),OK\r\n\n"
*@description: Los comandos que son consulta no poseen respuesta de comando recibido. Envian datos consultados.
*/
/************************************************
 *  CONFIGURACIÓN CANALES
		LED 1 (DAC_CHANNEL_1) --> Exitación horizontal
		LED 2 (DAC_CHANNEL_2) --> Exitación vertical
		Canal horizontal: canal1 - htim4
		Canal vertical: canal2 - htim5
 ***********************************************/
	{	switch ((uint8_t) new_cmd.name)
						{
				case CMD_CONFIG:
							{
								vTaskSuspend(RxTaskHandle);
								//!seteo led 1(horizontal)
								//uint16_t led_lvl = 4095 * new_cmd.params[0] / 100;
								led_lvl = 4095 * new_cmd.params[0] / 100;
								if (led_lvl>4095)
									led_lvl=4095;
								polarimeter.led1_power = led_lvl;
								HAL_DAC_SetValue(&hdac, DAC_CHANNEL_1, DAC_ALIGN_12B_R,led_lvl);
								
								//!seteo led 2
								led_lvl = 4095 * new_cmd.params[1] / 100;
								if (led_lvl>4095)
									led_lvl=4095;
								polarimeter.led2_power = led_lvl;
								HAL_DAC_SetValue(&hdac, DAC_CHANNEL_2, DAC_ALIGN_12B_R, led_lvl);
								
								//!Apago Leds
								HAL_DAC_SetValue(&hdac, DAC_CHANNEL_1, DAC_ALIGN_12B_R,0);
								HAL_DAC_SetValue(&hdac, DAC_CHANNEL_2, DAC_ALIGN_12B_R,0);
								
								/************************************************
							 *  @descriptionSeteo Voltaje de Fuentes
							 ***********************************************/
								//*Fuente 1
								uint8_t aux[4];
								polarimeter.hv1_power=new_cmd.params[2];
								aux2 = polarimeter.hv1_power*0.55187;
								conversion=round(aux2);
								sprintf((char*)aux,"%02X", conversion & 0x0000ffff);
								hps_sendcmd(&huart3, HBV,aux, 4);
								HAL_Delay(100);
								//*Fuente Dos
								polarimeter.hv2_power=new_cmd.params[3];
								aux2 = polarimeter.hv2_power*0.55187;
								conversion=round(aux2);
								sprintf((char*)aux,"%02X", conversion & 0x0000ffff);
								hps_sendcmd(&huart5, HBV,aux, 4); 
								HAL_Delay(100);
								
								//!@description:Respuesta CONFIG Correcto
								uint8_t res[14]="$RCONFIG\r\n";
								HAL_UART_Transmit(&huart6,res,sizeof(res),100);
								
								command_input.name=CMD_NULL;
								vTaskResume(RxTaskHandle);
								break;
							}
							case READ_POL:
							{/************************************************
							 *  @description:Calculo de mili Polarizacion
							 ***********************************************/
								vTaskSuspend(RxTaskHandle);
								measure(n, dt, t_off);
								pol= calc_polarization(lv_h_prom-new_cmd.params[2],lv_v_prom-new_cmd.params[3],lh_h_prom-new_cmd.params[0],lh_v_prom-new_cmd.params[1]);
								uint8_t len = sprintf((char*)uart_tx_buffer,"$RPOL,%d\r\n",(int)(pol*1000.0));
								sprintf((char*)uart_tx_buffer,"$RPOL,%d\r\n",(int)(pol*1000.0));
								HAL_UART_Transmit(&huart6,(uint8_t*) uart_tx_buffer,len,100);
								
								command_input.name=CMD_NULL;
								vTaskResume(RxTaskHandle);
							break;
							}
							case READ_ZERO:
							{/************************************************
								*  @description:Calculo de valores para "Calibracion"(Conteo de pulsos sin muestraso patron)
							 ***********************************************/
							vTaskSuspend(RxTaskHandle);
							if (new_cmd.params_number >= 1)
							{
								/*Para debug cometado
								uint16_t n = new_cmd.params[0]; 	// cantidad de muestas
								uint16_t dt = new_cmd.params[1]; 	//tiempo led on
								uint8_t t_off = new_cmd.params[2];//tiempo led off
								*/
								
								measure(n, dt, t_off);
								command_input.name=CMD_NULL;
								vTaskResume(RxTaskHandle);
							}else
								{
								polarimeter.lh_h_zero = 0;
								polarimeter.lh_v_zero = 0;
								polarimeter.lv_h_zero = 0;
								polarimeter.lv_v_zero = 0;
								}
								uint8_t len = sprintf((char*)uart_tx_buffer,"$RZERO,%d,%d,%d,%d\r\n", polarimeter.lh_h_zero, polarimeter.lh_v_zero,
																								 polarimeter.lv_h_zero, polarimeter.lv_v_zero);
							
								HAL_UART_Transmit(&huart6,(uint8_t*) uart_tx_buffer,len,100);
								
								command_input.name=CMD_NULL;
								vTaskResume(RxTaskHandle);
							break;
							}
							case SET_GFACTOR:
							{/************************************************
							 *  Seteo Gfactor
							 ***********************************************/
								vTaskSuspend(RxTaskHandle);
								if (new_cmd.params_number > 0){
									polarimeter.g_factor = (float) new_cmd.params[0]/1000.0;
									uint8_t res[14]="$SGFAC,OK\r\n";
									HAL_UART_Transmit(&huart6,res,sizeof(res),100);
									command_input.name=CMD_NULL;
								}
								vTaskResume(RxTaskHandle);
								break;
							}
							case READ_COVER:
							{/************************************************
							 *  Estado de error(Envio comando de error)
							 *	@description: Respuesta a consulta tapa abierta o cerrada
							 ***********************************************/
								vTaskSuspend(RxTaskHandle);
								uint8_t btnSts= HAL_GPIO_ReadPin(GPIOA, COVER_Pin);
								if(btnSts==0){
									uint8_t word[12]="$RCOVER,0\r\n";
									HAL_UART_Transmit(&huart6,word,sizeof(word),100);
								}else if(btnSts==1){
									uint8_t word[12]="$RCOVER,1\r\n";
									HAL_UART_Transmit(&huart6,word,sizeof(word),100);
								}

								command_input.name=CMD_NULL;
								vTaskResume(RxTaskHandle);
								break;
							}
							case CMD_ERROR:
							{/************************************************
							 *  Estado de error(Envio comando de error)
							 ***********************************************/
								//!@description: Aviso Error a Recepcion de Comando
								vTaskSuspend(RxTaskHandle);
								uint8_t word[21]="$RABORT\r\n";
								HAL_UART_Transmit(&huart6,word,sizeof(word),100);
								command_input.name=CMD_NULL;
								vTaskResume(RxTaskHandle);
								break;
							}
							case CMD_RESET:
							{
								vTaskSuspend(RxTaskHandle);
								NVIC_SystemReset();
								vTaskResume(RxTaskHandle);
								break;
							}
							case CMD_NULL:
							{
							break;
							}
						}
}

void HAL_UART_RxCpltCallback(UART_HandleTypeDef *huart)
{
	
	if (huart->Instance == huart3.Instance)
	{
		uart3_buffer[uart3_buffer_index] = new_char_uart3;
		if (uart3_buffer_index < sizeof(uart3_buffer) - 1)
			uart3_buffer_index++;
	}
	else if (huart->Instance == huart5.Instance)
	{
		uart5_buffer[uart5_buffer_index] = new_char_uart5;
		if (uart5_buffer_index < sizeof(uart5_buffer) -1)
			uart5_buffer_index++;
	}
	else if (huart->Instance == huart6.Instance)
	{
		if (new_char == COM_CHAR)
		{
			memset(uart_cmd_buff,'\0',sizeof(uart_cmd_buff));
			uart_cmd_buff[0] = new_char;
			uart_cmd_buff_index =0;
		}
		else
		{
			if(uart_cmd_buff_index < UART_CMD_BUFFER_LENGTH)
				uart_cmd_buff_index++;
			else
				uart_cmd_buff_index = 0;
			
			uart_cmd_buff[uart_cmd_buff_index] = new_char;
		}
	}
	command_input = comm_parse(uart_cmd_buff);
}	
/* USER CODE END 0 */

/**
  * @brief  The application entry point.
  * @retval int
  */
int main(void)
{
  /* MCU Configuration--------------------------------------------------------*/

  /* Reset of all peripherals, Initializes the Flash interface and the Systick. */
  HAL_Init();

  /* Configure the system clock */
  SystemClock_Config();

  /* Initialize all configured peripherals */
  MX_GPIO_Init();
  MX_DMA_Init();
  MX_ADC1_Init();
  MX_DAC_Init();
  MX_TIM4_Init();
  MX_TIM5_Init();
  MX_TIM2_Init();
  MX_UART5_Init();
  MX_USART3_UART_Init();
  MX_USART6_UART_Init();
  /* USER CODE BEGIN 2 */
  __HAL_UART_ENABLE_IT(&huart6,UART_IT_TC);
	HAL_UART_Receive_DMA (&huart6, &new_char, 1);
	HAL_DAC_SetValue(&hdac, DAC_CHANNEL_1, DAC_ALIGN_12B_R, 0);
  HAL_DAC_Start(&hdac, DAC_CHANNEL_1);
  HAL_DAC_SetValue(&hdac, DAC_CHANNEL_2, DAC_ALIGN_12B_R, 0);
  HAL_DAC_Start(&hdac, DAC_CHANNEL_2);
	hps_sendcmd(&huart3, HOF,NULL, 0);
	hps_sendcmd(&huart5, HOF,NULL, 0);

  /* USER CODE END 2 */

  /* USER CODE BEGIN RTOS_MUTEX */
  /* add mutexes, ... */
  /* USER CODE END RTOS_MUTEX */

  /* USER CODE BEGIN RTOS_SEMAPHORES */
  /* add semaphores, ... */
  /* USER CODE END RTOS_SEMAPHORES */

  /* USER CODE BEGIN RTOS_TIMERS */
  /* start timers, add new ones, ... */
  /* USER CODE END RTOS_TIMERS */

  /* USER CODE BEGIN RTOS_QUEUES */
  /* add queues, ... */
  /* USER CODE END RTOS_QUEUES */

  /* Create the thread(s) */
  /* definition and creation of defaultTask */
  osThreadDef(defaultTask, StartDefaultTask, osPriorityNormal, 0, 128);
  defaultTaskHandle = osThreadCreate(osThread(defaultTask), NULL);

  /* definition and creation of RxTask */
  osThreadDef(RxTask, RXTaskHandler, osPriorityNormal, 0, 128);
  RxTaskHandle = osThreadCreate(osThread(RxTask), NULL);

  /* USER CODE BEGIN RTOS_THREADS */
  /* add threads, ... */
  /* USER CODE END RTOS_THREADS */

  /* Start scheduler */
  osKernelStart();

  /* We should never get here as control is now taken by the scheduler */
  /* Infinite loop */
  /* USER CODE BEGIN WHILE */
  while (1)
  {		
    /* USER CODE END WHILE */

    /* USER CODE BEGIN 3 */
  }
  /* USER CODE END 3 */
}

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
/* USER CODE BEGIN Header_StartDefaultTask */
/**
  * @brief  Function implementing the defaultTask thread.
  * @param  argument: Not used
  * @retval None
  */
/* USER CODE END Header_StartDefaultTask */
void StartDefaultTask(void const * argument)
{
  /* USER CODE BEGIN 5 */
	
  
	/* Infinite loop */
  for(;;)
  {
		data(command_input);
		
  }
  /* USER CODE END 5 */
}

/* USER CODE BEGIN Header_RXTaskHandler */
/**
* @brief Function implementing the RxTask thread.
* @param argument: Not used
* @retval None
*/
/* USER CODE END Header_RXTaskHandler */
void RXTaskHandler(void const * argument)
{
  /* USER CODE BEGIN RXTaskHandler */
  /* Infinite loop */
  for(;;)
  {
		HAL_UART_Receive_DMA(&huart6,&new_char,1);
  }
  /* USER CODE END RXTaskHandler */
}

/**
  * @brief  Period elapsed callback in non blocking mode
  * @note   This function is called  when TIM10 interrupt took place, inside
  * HAL_TIM_IRQHandler(). It makes a direct call to HAL_IncTick() to increment
  * a global variable "uwTick" used as application time base.
  * @param  htim : TIM handle
  * @retval None
  */
void HAL_TIM_PeriodElapsedCallback(TIM_HandleTypeDef *htim)
{
  if (htim->Instance == TIM10) {
    HAL_IncTick();
  }
}

/**
  * @brief  This function is executed in case of error occurrence.
  * @retval None
  */
void Error_Handler(void)
{
  /* USER CODE BEGIN Error_Handler_Debug */
  /* User can add his own implementation to report the HAL error return state */

  /* USER CODE END Error_Handler_Debug */
}

#ifdef  USE_FULL_ASSERT
/**
  * @brief  Reports the name of the source file and the source line number
  *         where the assert_param error has occurred.
  * @param  file: pointer to the source file name
  * @param  line: assert_param error line source number
  * @retval None
  */
void assert_failed(uint8_t *file, uint32_t line)
{
  /* USER CODE BEGIN 6 */
  /* User can add his own implementation to report the file name and line number,
     tex: printf("Wrong parameters value: file %s on line %d\r\n", file, line) */
  /* USER CODE END 6 */
}
#endif /* USE_FULL_ASSERT */

/************************ (C) COPYRIGHT STMicroelectronics *****END OF FILE****/

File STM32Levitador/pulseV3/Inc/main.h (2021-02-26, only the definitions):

#define COUNTER_PMT_2_Pin GPIO_PIN_0
#define COUNTER_PMT_2_GPIO_Port GPIOA
#define LED_PWR_1_Pin GPIO_PIN_4
#define LED_PWR_1_GPIO_Port GPIOA
#define LED_POWER_2_Pin GPIO_PIN_5
#define LED_POWER_2_GPIO_Port GPIOA
#define LED_LVL_1_Pin GPIO_PIN_6
#define LED_LVL_1_GPIO_Port GPIOA
#define LED_LVL_2_Pin GPIO_PIN_7
#define LED_LVL_2_GPIO_Port GPIOA
#define BT1_Pin GPIO_PIN_0
#define BT1_GPIO_Port GPIOB
#define BT2_Pin GPIO_PIN_1
#define BT2_GPIO_Port GPIOB
#define BT3_Pin GPIO_PIN_2
#define BT3_GPIO_Port GPIOB
#define PSU_CTRL_1_Pin GPIO_PIN_11
#define PSU_CTRL_1_GPIO_Port GPIOB
#define PSU_STS_1_Pin GPIO_PIN_12
#define PSU_STS_1_GPIO_Port GPIOB
#define PSU_CTRL_2_Pin GPIO_PIN_14
#define PSU_CTRL_2_GPIO_Port GPIOB
#define PSU_STS_2_Pin GPIO_PIN_15
#define PSU_STS_2_GPIO_Port GPIOB
#define COVER_Pin GPIO_PIN_8
#define COVER_GPIO_Port GPIOA
#define COUNTER_PMT_1_Pin GPIO_PIN_6
#define COUNTER_PMT_1_GPIO_Port GPIOB

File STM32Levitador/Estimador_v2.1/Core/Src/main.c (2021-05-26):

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
/* Includes ------------------------------------------------------------------*/
#include "main.h"

/* USER CODE BEGIN Includes */
#include <stdio.h>
#include <stdlib.h>
#include <string.h>
#include <math.h>
#include "muestras.h"
#include "fdacoefs.h"
#include "fda_derivador.h"

/* USER CODE END Includes */

/* USER CODE BEGIN PM */
#define min(a,b) (((a)<(b))?(a):(b))
#define max(a,b) (((a)>(b))?(a):(b))
/* USER CODE END PM */

ADC_HandleTypeDef hadc1;
DMA_HandleTypeDef hdma_adc1;

TIM_HandleTypeDef htim2;
TIM_HandleTypeDef htim3;
TIM_HandleTypeDef htim4;

UART_HandleTypeDef huart1;

/* USER CODE BEGIN PV */
volatile uint16_t counter = 0;
const int pwmGain = 800;
volatile int8_t sign = 1;
uint16_t numViL;

uint16_t tStart, tEnd, tTotal;

uint8_t printSerial = 0;
uint32_t tLast = 0;
const uint8_t printInterval = 20;		//20 ms

#define adcSamples 100
uint16_t adcBuf[adcSamples];

volatile uint16_t adcVal[2];
#define numSamples  adcSamples / 2

uint16_t adc_ch0[numSamples];
uint16_t adc_ch1[numSamples];

volatile uint8_t adcConverted = 0;
/*const uint16_t fs = 50000;
const float RL = 0.2;
const float L_4mm = 16.2e-3;
float ViL[numSamples];
float IL[numSamples];
float ILmed;
float deltaIL;
float derivadas[numSamples];
float Yestimada[numSamples];
float Yestimada_promedio;
*/

const int fixedPointGain = 1000;
const uint16_t fs = 50000;
const float RL = 0.2;
const float L_4mm = 16.2e-3;
const float Kh = 0.05;				//transductancia del sensor de efecto Hall
uint16_t vilIndex = 0;
#define N_ADC 16
const int n = N_ADC - 1;
uint16_t muestrasHall[N_ADC];
uint16_t muestrasRef[N_ADC];
int32_t muestrasADC[N_ADC];
int32_t IL[N_ADC];
int32_t ILmed;
float deltaIL;
int16_t derivadas[N_ADC];
int32_t derivadas_filtrada[N_ADC];
int32_t Yestimada[N_ADC];
int32_t Yestimada_filtrada[N_ADC];

void getViL(float * ViL, uint16_t * adc){
	float res = 3.3 / 4096;
	for(int i = 0; i < numSamples; i++){
		ViL[i] = adc[i] * res;
	}
}

float corriente(float Xn){
		return Xn / Kh;
}

float corriente_media(float * IL){
	float sum = 0;
	for(int i = 0; i<numSamples; i++){
		sum += IL[i];
	}
	return sum/numSamples;
}

float delta_corriente(float * IL){
	float ILmax = 0;
	float ILmin = 100;
	for(int i= 0; i<numSamples; i++){
		ILmax = max(IL[i], ILmax);
		ILmin = min(IL[i], ILmin);
	}
	return ILmax - ILmin;
}

int16_t derivar(uint16_t * muestrasHall){
	int16_t deriv = (muestrasHall[n] - muestrasHall[n - 1]);	//acá tengo la diferencia en el número que lee el adc
//	deriv += ILmed * 0.05 * RL / L_4mm;			//corrección I * R
	return deriv;
}

float estimar(int16_t derivada){
		float estim = abs(derivada) * 4.74e-3 - 4.55e-3;
		if(estim < 800e-3)
			return estim;
		else
			return 8e-3;						//esto lo hago para que la primera muestra no sea tan erronea
}

float filtrar(float * X, const float * B){			//acá la Y significa la salida del filtro, no la posición en mm
	float out = 0;
	for (int i = 0; i < N_ADC; i++) {				//acá aplico el filtro
		out += B[i] * X[n - i];			//B son los coeficientes de un filtro FIR
	 }
	 return out;
}

float promediar(float * Yestimada){
	float sum = 0;
	for(int i = 0; i < numSamples; i++){
		sum += Yestimada[i];
	}
	return sum / numSamples;
}

/* USER CODE END PV */

void SystemClock_Config(void);
static void MX_GPIO_Init(void);
static void MX_DMA_Init(void);
static void MX_TIM3_Init(void);
static void MX_TIM4_Init(void);
static void MX_ADC1_Init(void);
static void MX_TIM2_Init(void);
static void MX_USART1_UART_Init(void);
/**
  * @brief  The application entry point.
  * @retval int
  */
int main(void)
{
  /* MCU Configuration--------------------------------------------------------*/

  /* Reset of all peripherals, Initializes the Flash interface and the Systick. */
  HAL_Init();

  /* Configure the system clock */
  SystemClock_Config();

  /* Initialize all configured peripherals */
  MX_GPIO_Init();
  MX_DMA_Init();
  MX_TIM3_Init();
  MX_TIM4_Init();
  MX_ADC1_Init();
  MX_TIM2_Init();
  MX_USART1_UART_Init();
  /* USER CODE BEGIN 2 */
  /*
  //esto es para generar una señal de prueba en pwm. Se puede anular esta parte cuando hacemos pruebas en la placa real
   HAL_TIM_PWM_Start(&htim2, TIM_CHANNEL_1);
   HAL_TIM_Base_Start_IT(&htim4);
   //uint16_t loopDelay = 1;
    numViL = sizeof(ViLmuestras)/sizeof(ViLmuestras[0]);
    int loopCount = 0;
 */

   //cosas del adc
   HAL_TIM_Base_Start(&htim3);				//inicio el timer 3 para comenzar las conversiones del ADC
   HAL_ADC_Start_DMA(&hadc1, (uint32_t *) adcVal, 2);			//inicio adc dma
       	  	  	  	  	  	  	  	  	  	  	  	  	  	  	//para que lea la cantidad numSamples
   	  	  	  	  	  	  	  	  	  	  	  	  	  	  	  	//y luego dispare una interrupción
   //para medir el tiempo que tarda en ejecutar el código
   HAL_TIM_Base_Start(&htim4);

  /* USER CODE END 2 */

  /* Infinite loop */
  /* USER CODE BEGIN WHILE */
  while (1)
  {
    /* USER CODE END WHILE */

    /* USER CODE BEGIN 3 */

	  if(adcConverted){
		 tStart = __HAL_TIM_GET_COUNTER(&htim4);		//para calcular el tiempo que tarda
		 adcConverted = 0;								//reseteo el flag del adc
		// HAL_TIM_Base_Stop(&htim3);			//paro el timer del adc (esto es temporal)
		// HAL_GPIO_TogglePin(led_GPIO_Port, led_Pin);		//esto es para ver la frecuencia de muestreo

		 //esto es para separar las muestras del canal 1 y el 2
		 //leo la muestra de corriente y la pongo al final del array del sensor de efecto hall
		  muestrasHall[n] = adcVal[0];
		  muestrasRef[n] = adcVal[1];

		  //convierto el valor del ADC en valor de tensión
		  //muestrasADC[n] = (muestrasHall[n] * 3.3 / 4096) / pwmGain;
		//  muestrasADC[n] = muestrasHall[n] * (8.056e-4 * fixedPointGain);	//3.3/4096 = 8.056e-4

		//  IL[n] = corriente(muestrasADC[n]);					//calculo el valor en corriente
		//  ILmed = (IL[n] + ILmed) / 2;							//añado al promedio movil
		  //deltaIL
		  derivadas[n]  = derivar(muestrasHall);			//calculo la derivada con la muestra anterior
		  //derivadas_filtrada[n] = filtrar(derivadas, Bderiv);	//filtro las derivadas obtenidas
		  Yestimada[n]  = estimar(derivadas[n]);
		  //Yestimada_filtrada[n] = filtrar(Yestimada, Bposicion);	//filtro

		  //acá paso todos los valores un lugar a la izquierda
		  //for (int i = n; i > 0; i--) {
				//muestrasHall[n - i] = muestrasHall[n - i + 1];
				//muestrasRef[n - i] = muestrasRef[n - i + 1];
				//muestrasADC[n - i] = muestrasADC[n - i + 1];
				//IL[n - i] = IL[n - i + 1];
				//derivadas[n - i] = derivadas[n - i + 1];
				//derivadas_filtrada[n - i] = derivadas_filtrada[n - i + 1];
				//Yestimada[n - i] = Yestimada[n - i + 1];
				//Yestimada_filtrada[n - i] = Yestimada_filtrada[n - i + 1];
		//	  }

		  muestrasHall[n - 1] = muestrasHall[n];
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

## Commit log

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2021-03-01 DMA en comm_interfaz
    En vez de usar interrupciones para recibir los bytes, uso DMA. el funcionamiento es el mismo
    [comm_interfaz Debug.cfg]
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2021-03-05 Modificación de los gráficos
    Anda bien, pero tiene un bug medio choto. Cuando grafico una vez, lo cierro y vuelvo a graficar, se interrumpe el programa
    [comm.c, main.c]
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2021-03-17 Revert "a"
    This reverts commit 2fcbf59904a7166787cba87a28c842cbfc7ab5ae.
    [comm_interfaz.ioc]
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2021-03-23 Cambio de operacionales en el controlador de corriente
    En vez de cambiar el TLV2464 por el MCP660, lo cambie por el MCP664, ya que el encapsulado tiene 4 operacionales en vez de 3, y la respuesta en frecuencia es la misma
    [Controlador de corriente V3.SchDoc]
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2021-03-25 Incluí la parte del estimador y correcciones en el controlador de corriente
    [Controlador de corriente V3.SchDoc, Estimador.SchDoc]
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2021-04-07 Cálculo de posición de referencia en estimador digital
    La posición de referencia se obtiene muestreando el canal 1 del ADC, al que le ingresa la señal del potenciómetro (con niveles de tensión adaptados de manera correcta), y se traduce esta tensión en un valor re posición de referencia.
    [comm_interfaz.ioc, compensador.c, main.c]
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2021-04-12 Modificaciones en esquemático de fuentes de alimentación
    Agregue el puerto para la señal de 3.3V, cambié de lugar las cosas del esquemático
    [Fuentes.SchDoc, Principal.SchDoc]
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2021-04-15 Reubiqué los capacitores de los transistores de conmutación y agregué algunas notas
    [Controlador de corriente V3.SchDoc, Fuentes.SchDoc, MB1136.PrjPCB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]
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2021-05-16 Creé la versión 2.0 para no borra lo esquemáticos que no vamos a usar
    [Compensador.SchDoc, Controlador de corriente V3.SchDoc, Controlador de corriente V2.SchDoc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]
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2021-06-07 Resetee los designator y acomodé algunas cosas
    [Controlador de corriente V3.SchDoc, Estimador.SchDoc, Fuentes.SchDoc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]
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2021-06-22 Agregué footprint para header de entrada de 24V y el del electroimán
    [levitador_original.PcbLib]
2021-07-22 Quité los diodos en paralelo a los MOS y los del Source
    [Controlador de corriente V3.SchDoc, Estimador.SchDoc]
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2021-08-22 Agregué el Schmitt-Trigger Inverter por partes y lo puse en el controlador de corriente
    [Controlador de corriente V3.SchDoc, Levitador_GMI.PcbLib, Levitador_GMI.SchLib]
2021-08-22 Agregué la polaridad al footprint de los capacitores de fuente de 24V
    [Controlador de corriente V3.SchDoc, Levitador_GMI.PcbLib, Levitador_GMI.SchLib]
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2021-10-12 Acomodé esquemático controlador de corriente
    Corregí un operacional que estaba al revés, acomodé un poco las cosas. faltarían un par de cositas... yo achicaría el simbolo del sensor de efecto hall
    [Controlador de corriente V3.SchDoc]
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2021-10-15 Cambios en el estimador de posición - Filtro pasa bajos de entrada
    [Control Levitador.SchDoc, Estimador.SchDoc]
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2021-10-18 Nuevo archivo de simulación del controlador de corriente
    Hice un archivo nuevo por que el anterior tenía algunos errores
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2021-11-04 Creación del PCB y corrección de errores
    [Controlador de corriente V3.SchDoc, Estimador.SchDoc, LevitadorMagnetico.PcbDoc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]
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2021-11-16 Ruteo de fuentes
    Es un ruteo aproximado para ver como quedarían las conexiones. Para hacer el ruteo posta hay que hacer mas anchas las pistas, evitar que tenga angulos rectos, etc
    [LevitadorMagnetico.PcbDoc]
2021-11-16 Fuentes
    Agrande Pistas de fuentes y corri los leds para que esten alineados todes.
    PD: no se poruqe no puedo hacerle repour a los planos. capaz que es por algo de la version de altium.
    [LevitadorMagnetico.PcbDoc]
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2021-11-16 Ruteo de mas CC
    Hay que ubicarlo bien en la placa, acomodar algunos width de pistas y capaz q alienar algunos componentes que quedaron mal XD
    [LevitadorMagnetico.PcbDoc]
2021-11-16 Arreglé lo de los poligonos
    [LevitadorMagnetico.PcbDoc]
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2021-11-17 Ruteo de CC V2
    Ruteo de CC chequear que este todo OK y ver si les gusta. Lo lleve para abajo a la izquierda porq me quedo comodo de ultima desp se puede cambiar de lugar.
    [LevitadorMagnetico.PcbDoc]
2021-11-17 Ruteo de Signals2uc
    Puse masomenos para tener una idea de como iria la parte de signals2uc igualmete estaria mas piola definir primero el compensador. (por ahi darle espacio de mas por las dudas, por si hay que agregarl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
    [Signals2uC.SchDoc]
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2021-11-23 Corrección de los valores de los capacitores de Bootstrap y actualización TP102
    [Controlador de corriente V3.SchDoc]
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2021-11-24 Ruta++
    Ruteado todo(Creo). exagere con el vias stitching. corregi net´s duplicadas de +5.0V y +5V que habia. No compile para ver si quedo algun error ni nada Si pinta cambiar algo cambienlonn XD
    [Controlador de corriente V3.SchDoc, Estimador.SchDoc, Fuentes.SchDoc]
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2021-11-25 Revert "Cambios en poligonos del pcb"
    This reverts commit 3ee4110ab342748bacd8546fae619c35e374569e.
2021-11-25 Cambios en poligono de GND y se quitó el stitching de vias. También se modificó el overlay del footprint de los diodos para mostrar la orientación
    [Levitador_GMI.PcbLib]
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2021-11-27 Separamos el puente H en un nuevo esquemático y agregamos resistencias serie en los gates de los MOSFET
    [Compensador.SchDoc, Controlador de corriente V3.SchDoc, Fuentes.SchDoc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]
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2021-11-27 Soluciones de errores y warnings de esquemáticos
    [Compensador.SchDoc, Controlador de corriente V3.SchDoc, Estimador.SchDoc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]
2021-11-27 Independicé el operacional de la salida del sensor de efecto hall y coloqué algunos componentes en el nuevo PCB
    [Controlador de corriente V3.SchDoc, Levitador Magnetico.PcbDoc, Modelo levitador magnético.PrjPcb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]
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2021-12-02 Agregué una flechita en el footprint del sensor hall para indicar el sentido positivo de la corriente
    [Levitador_GMI.PcbLib]
2021-12-02 Cambio de lugar
    Esto es a modo de prueba para ver como quedarían. Los cambios que hice fue cambiar de lugar cada rama de transistores, los de la derecha los pasé a la izquierda, y así también los otros. Además di vu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
    [Puente H.SchDoc]
2021-12-02 Agregué comentario al footprint de los testpoints.
    Así ya aparece con el nombre de la señal. Después nos queda ocultar los designators
    [Levitador_GMI.PcbLib]
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2021-12-13 Agregue pista de 5V para que pasen todas las señales por el mismo lugar ver si pinta o no
    [Modelo levitador magnético.PrjPcb]
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2021-12-16 Altium Compensador acomodado en PCB
    Todo OK solo falta componentes del integrador// modificar reglas para que no tire error si pinta
    [Modelo levitador magnético.PrjPcb]
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2021-12-28 Corregidos algunos errores
    Quedan modificar el silk screen de los diodos para que sea mayor a 0.15
2021-12-29 Rule cheq y vias stitching
    No quedaron errores solo los del integradito chico y agregue vias stitching
    [Levitador_GMI.PcbLib]
2021-12-29 Agregado archivo simulink
    Para que ande hay que correr el archivo de compensador por adelanto de fase.m
    Igualmente hay un error de derivada en t=0 que no lo pude solucionar
2021-12-30 Modificación esquemático de compensador en la etapa del compensador de adelanto de fase
    [Compensador.SchDoc]
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2022-01-10 Corrección de signo de compensador y ganancia integrador.
    A partir de la simulación en simulink se verificó que esta es una forma correcta de ubicar los signos. Como tenemos un integrador, a la entrada de este el error será nulo, por lo tanto la referencia debe ser restada con la realimentación. Luego el integrador agrega una inversión de signo (debido a la implementación circuital) y este signo es invertido nuevamente en el restador de Verror2.
    Además modifiqué el valor de las resistencias R307 y R311.
    [Compensador.SchDoc]
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2022-01-12 Cambios en libreria en el Regulador de Tension(Solder Mask ) para evitar error de compilacion.
    [Fuentes.SchDoc, Levitador_GMI.PcbLib, Levitador_GMI.SchLib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]
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2022-03-30 Actualización de PCB
    Compilado esquemáticos
    Exportados los cambios de los esquemáticos al PCB
    Modificado el PCB con los nuevos cambios
    Re-ruteado
    Re-pour de polígonos
    Corregido Via stitching
    Design rule check sin errores
    [Controlador de corriente V3.SchDoc, Fuentes.SchDoc]
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2022-06-06 agregado de error en regimen permanente
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2022-11-15 Correccion error y agregado de cosas en tabla
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2022-12-12 Revert "cambios calculo de F para mapeo"
    This reverts commit f750ceaccca4438dc96f92e14cc29a3a16defe94.
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

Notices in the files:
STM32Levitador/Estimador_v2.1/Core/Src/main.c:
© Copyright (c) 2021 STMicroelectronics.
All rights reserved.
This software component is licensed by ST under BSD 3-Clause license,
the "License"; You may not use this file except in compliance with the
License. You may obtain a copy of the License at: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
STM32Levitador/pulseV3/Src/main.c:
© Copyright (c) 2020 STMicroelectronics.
